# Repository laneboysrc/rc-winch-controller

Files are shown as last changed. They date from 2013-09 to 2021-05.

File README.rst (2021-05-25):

DIY controller an RC car winch
==============================

This project is for a winch controller for Radio Controlled cars that uses
channel 3 to operate the winch remotely.

Usage
=====

Connect the winch controller to channel 3 of your receiver.

Three seconds after you apply power to the controller the winch motor will play
a short tune. The sound will only play if a valid input signal has been
detected. Note that the sound generated by the motor may be very faint depending on your
winch.

To arm the switch, change the position of the channel 3 switch on your
transmitter five times within a short period of times. The winch motor
will now play a different tune of rising sounds indicatiting that it is
armed. While armed, the winch motor will be braked electrically.

To move the winch in one direction, change the position of the channel 3
switch once. To move the winch in the other direction, change the position
of the channel 3 switch twice within a short time.

To stop the winch moving toggle the position of the channel 3 switch.

Hardware
========

The winch hardware is basically a H-bridge motor driver controlled from a
tiny microcontroller.

The winch controller can be powered via the RC receiver, or from a separate
supply connected to the pins labeled + an - on the ICSP connector.

The main components are a Microchip PIC 12F1840 microcontroller, two
dual N- and P-Channel power FETs Fairchild FDS9934C, and a 3.3V LDO
(Microchip MCP1702, 1703 or similar).

A common 1/10th scale RC winch can lift about 1.5 kg at 6 Volts. The maxium
current we measured on our winch is 800 mA.

The schematics and a PCB layout are available in the `electronics <electronics/>`_ folder.

Bill of material:

::

    Qty Value            Device               Parts
    1   PIC12F1840       PIC12F1840 S08       U$2
    2   FDS9934          P/N MOSFET SO8       T1, T2
    1   MCP1702-3302     LDO 3V3 SOT23        U$1
    2   MMTB2222         NPN-TRANSISTOR SOT23 Q1, Q2
    2   1uF/16V          Capacitor SMD 1206   C1, C2
    1   0R               Resistor SMD 0603    R9 (can be replced with a solder bridge)
    6   4k7              Resistor SMD 0603    R1, R2, R3, R4, R7, R8
    2   47k              Resistor SMD 0603    R5, R6

The 2-layer PCB size is 22.05 x 27.43 mm (0.87 x 1.08 inches).

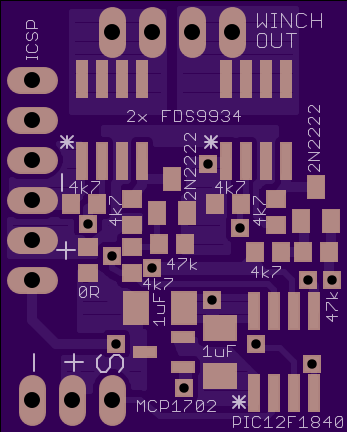
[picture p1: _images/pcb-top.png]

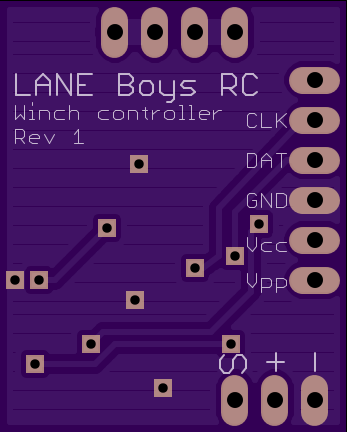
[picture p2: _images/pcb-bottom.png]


Gerber files for the PCB can be found in the `electronics <electronics/>`_ folder. The PCB can be
`ordered directly from OSHPark <http://www.oshpark.com>`_ in a minimum quantity of three.

Software
========

The firmware has been developed using SDCC version 3.3 and gpasm version 1.0.
GNU make is required for the build.

If you are compiling the software on a computer that does not have Unix-like
tools installed (e.g. Microsoft Windows) then you may need to adapt the
rm utility referenced in the Makefile (i.e. use "del" instead of "rm").

For convenience a pre-compiled HEX file is available for download `here <firmware/rc-winch-controller-servo.hex>`_.

The firmware comes in two variants: One that connects to channel 3 of a
RC receiver, and one with UART input which is meant to be utilized in
conjunction with the `LANE Boys RC DIY RC Light controller <http://laneboysrc.blogspot.com/2012/07/diy-car-light-controller-for-3-channel.html>`_.

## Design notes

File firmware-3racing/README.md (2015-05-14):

This folder contains firmware for the 3-Racing winch controller so
that it can be used with a 2-position switch.

The original 3-Racing winch controller works with a transmitter that has
a 3-position switch on CH3.

This firmware hooks in-between the receiver output and the 3-Racing winch
controller. It reads the CH3 2-pos switch info from the receiver and on
change of the switch outputs a servo signal simulating a 3-position switch.

After power on the winch is off. Every CH3 change modifies the servo
signal output to the 3-Racing controller:

Off         1500us
Winch out   2000us
Off         1500us
Winch in    1000us
Off         1500us
Winch out   2000us
...

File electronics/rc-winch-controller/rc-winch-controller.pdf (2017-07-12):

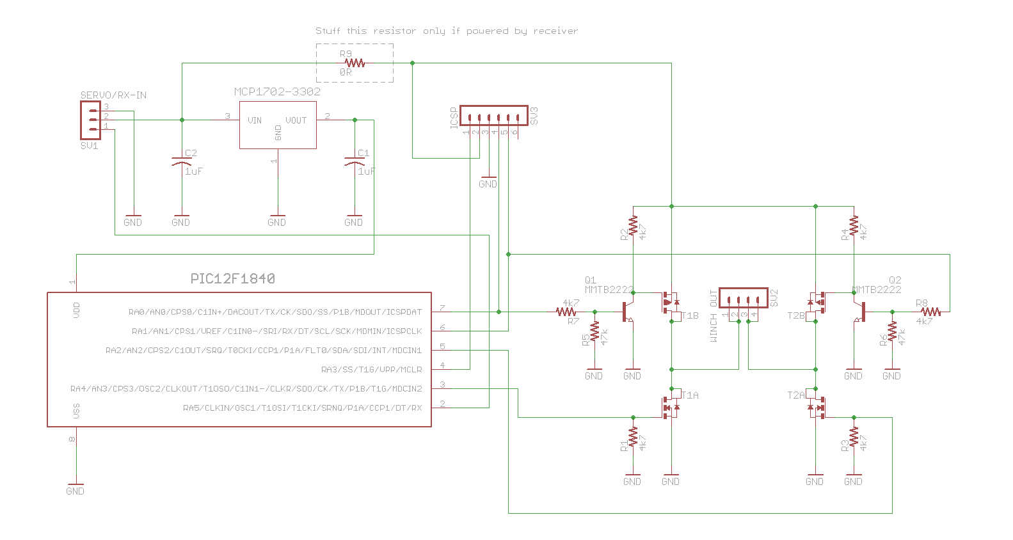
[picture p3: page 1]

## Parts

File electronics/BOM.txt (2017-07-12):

Part        Value              Package    Description
=============================  ========================================================
C1          1uF/16V            C1206K     CAPACITOR
C2          1uF/16V            C1206K     CAPACITOR
Q1          MMTB2222           SOT23      NPN TRANSISTOR
Q2          MMTB2222           SOT23      NPN TRANSISTOR
R1          4k7                R0603      RESISTOR
R2          4k7                R0603      RESISTOR
R3          4k7                R0603      RESISTOR
R4          4k7                R0603      RESISTOR
R5          47k                R0603      RESISTOR
R6          47k                R0603      RESISTOR
R7          4k7                R0603      RESISTOR
R8          4k7                R0603      RESISTOR
R9          0R                 R0603      RESISTOR
SV1         SERVO/RX-IN                   PIN HEADER
SV2         WINCH OUT                     PIN HEADER (optional)
SV3         ICSP                          PIN HEADER (optional)
T1          FDS9934            SO8        DUAL N AND P-CHANNEL ENHANCEMENT MODE MOSFET
T2          FDS9934            SO8        DUAL N AND P-CHANNEL ENHANCEMENT MODE MOSFET
U$1         MCP1702T-3302E/CB  SOT-23A
U$2         PIC12F1840         SO8        Microchip PIC12F1840

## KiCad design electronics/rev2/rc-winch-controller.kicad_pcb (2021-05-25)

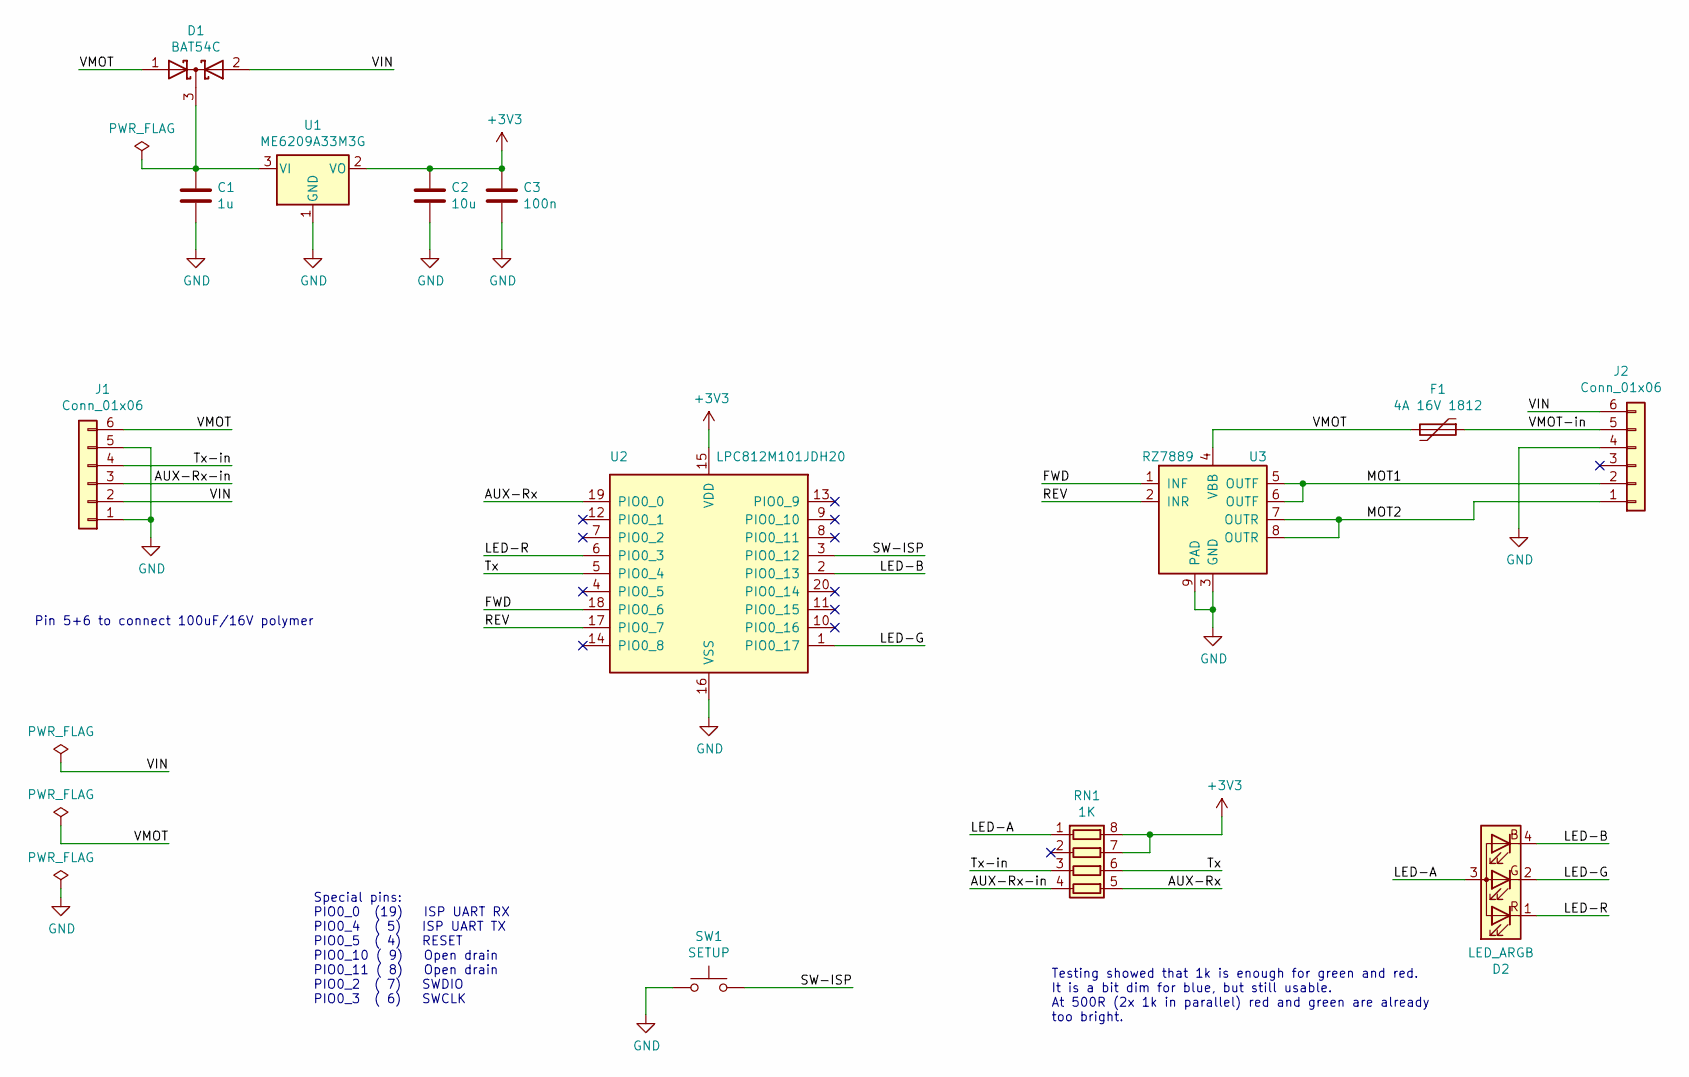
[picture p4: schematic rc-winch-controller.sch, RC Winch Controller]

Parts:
C1: 1u; C_0805_2012Metric
C2: 10u; C_0805_2012Metric
C3: 100n; C_0603_1608Metric
D1: BAT54C; SOT-23
D2: LED_ARGB; LED_RGB_XINGLIGHT_XL-2012RGBC
F1: 4A 16V 1812; Fuse_1812_4532Metric_Pad1.30x3.40mm_HandSolder
J1, J2: Conn_01x06; PinHeader_1x06_P2.54mm_Flat
RN1: 1K; R_Array_Convex_4x0603
SW1: SETUP; Tact switch 6x4x3
U1: ME6209A33M3G; SOT-23W
U2: LPC812M101JDH20; TSSOP-20_4.4x6.5mm_P0.65mm
U3: RZ7889; SOIC-8-1EP_3.9x4.9mm_P1.27mm_EP2.29x3mm_ThermalVias

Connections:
+3V3: C2.1, C3.1, RN1.7 (R2.2), RN1.8 (R1.2), U1.2 (VO), U2.15 (VDD)
/AUX-Rx: RN1.5 (R4.2), U2.19 (PIO0_0)
/AUX-Rx-in: J1.3, RN1.4 (R4.1)
/FWD: U2.18 (PIO0_6), U3.1 (INF)
/LED-A: D2.3 (A), RN1.1 (R1.1)
/LED-B: D2.4 (BK), U2.2 (PIO0_13)
/LED-G: D2.2 (GK), U2.1 (PIO0_17)
/LED-R: D2.1 (RK), U2.6 (PIO0_3)
/MOT1: J2.2, U3.5 (OUTF), U3.6 (OUTF)
/MOT2: J2.1, U3.7 (OUTR), U3.8 (OUTR)
/REV: U2.17 (PIO0_7), U3.2 (INR)
/SW-ISP: SW1.2, U2.3 (PIO0_12)
/Tx: RN1.6 (R3.2), U2.5 (PIO0_4)
/Tx-in: J1.4, RN1.3 (R3.1)
/VIN: D1.2 (A), J1.2, J2.6
/VMOT: D1.1 (A), F1.2, J1.6, U3.4 (VBB)
/VMOT-in: F1.1, J2.5
GND: C1.2, C2.2, C3.2, J1.1, J1.5, J2.4, SW1.1, U1.1 (GND), U2.16 (VSS), U3.3 (GND), U3.9 (PAD)
unnamed: C1.1, D1.3 (K), U1.3 (VI)

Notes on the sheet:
Special pins: PIO0_0 (19) ISP UART RX PIO0_4 ( 5) ISP UART TX PIO0_5 ( 4) RESET PIO0_10 ( 9) Open drain PIO0_11 ( 8) Open drain PIO0_2 ( 7) SWDIO PIO0_3 ( 6) SWCLK
Testing showed that 1k is enough for green and red. It is a bit dim for blue, but still usable. At 500R (2x 1k in parallel) red and green are already too bright.
Pin 5+6 to connect 100uF/16V polymer

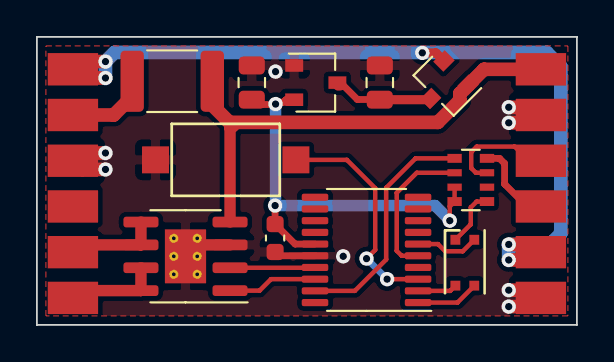
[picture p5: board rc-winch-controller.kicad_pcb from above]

Board: 2 copper layers, 30.0 x 16.0 mm, 13 parts (0 on the bottom side), 19 nets.

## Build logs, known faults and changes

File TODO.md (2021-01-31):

# Ideas for Mk2

* Up to 3S operation (12.6V)
* LEDs and push-button for configuration
* Inputs
    - Servo input 3-pos switch
    - Servo input 2-pos switch
    - External 3-pos switch
    - External 2-pos switch
    - External push-button (any difference from 2-pos switch?)
    - Internal push-button
    - Light Controller protocol
* Arming function
    * Can be disabled in the settings
    * Applies to all input modes except Light Controller
* Configurable motor reversal
    * Do we need that? User can just plug in the motor the other way around ...
* Firmware update
    * Hold button to start
* Configurable safety timeout for motor running
* Mini-ESC mode
    - 8 kHz to 16 kHz PWM frequency?
    - Drag brake adjustable?
    - Different modes: F/B/R, Crawler mode, F/B?
    - End-point learning
    - Channel reversing
    - Punch?

## Building blocks

* LPC812 16p (or QFN?)
* Use Wuxi RZ7899 or RZ7889 motor driver
* LDO 3V3
* 100uF polymer 16V 5x9mm
* Low-cost 3.3V-side buffer cap? 10u MLCC?
* Pushbutton
* External 2-pos switch connects to S/RX - GND
* External 3-pos switch connects to S/RX - Tx - GND
* RGB LED
* Power input
    * Allow various combinatoins:
        * Motor and electronics powered from servo connector
        * Motor and electronics powered from external supply
        * Motor powered from external supply, electronics powered from servo connector
    * Feed MCU from BAT54C! SOT-23
        * Motor-side use 6p connector with same jumper arrangement as on Mk4P/Mk4S

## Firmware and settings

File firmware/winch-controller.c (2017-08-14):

#include <pic12f1840.h>
#include <stdint.h>

static __code uint16_t __at (_CONFIG1) configword1 = _FOSC_INTOSC & _WDTE_OFF & _PWRTE_ON & _MCLRE_OFF & _CP_OFF & _CPD_OFF & _BOREN_OFF & _CLKOUTEN_OFF & _IESO_OFF & _FCMEN_OFF;
static __code uint16_t __at (_CONFIG2) configword2 = _WRT_OFF & _PLLEN_OFF & _STVREN_OFF & _LVP_OFF;


/*

Pin 7   RA0/ICSPDAT = High side left
Pin 6   RA1/ICSPCLK = High side right
Pin 5   RA2/CCP1  = Low side right (CCP1 for music!)
Pin 4   RA3/Vpp goes to ICSP
Pin 3   RA4 = Low side left
Pin 2   RA5/RX = Servo/UART Input

Music that the controller makes
===============================
- Startup sound
- Off to idle transition
- Idle to off transition


Playing a "song" through the motor
==================================

Single tones are generated by a PWM of 50% at the frequency of the sound.
A "song" comprises of individual notes, each note has a duration.
Between notes there can be pauses of a given duration.

Music notes go from 16.35 Hz to 4978.03 Hz according to
http://www.phy.mtu.edu/~suits/notefreqs.html
C3 to C5 (a smaller scale probably is enough) from 130.81 to 523.25 Hz
Maybe the best is to encode the musical note (there are 12 notes in an
octave) and have a table that has pre-calculated timer values for
the reqired frequency.

130.81 Hz (C3) -> 7645 us period = 3823 us half period
440 Hz (A4) -> 2273 us period = 1136 us half period
2093 Hz (C7) -> 478 us period = 239 us half period

If we allow for 4..1020 ms tone / pause durations (8 bits with 4ms resolution)
we need to decrement the "tone counter" every 4,096 ms. We can do that
reasonably accurate by accumulating an 8 bit value with a 16us resolution.
So at each interrupt we would add the number of "16us units" to our counter.
If it  overflows we decrement the tone counter. This way we should be able to
account for reasonably accurate tone durations regardless of the
note frequency.

If we use Timer1 for music we will not be able to output music at the
same time as measuring a servo pulse. This should not pose an issue
if the songs we play are short, and we can make the software stop while
the songs are playing.

We use Timer1 and CCP1 in compare mode. CCP1 is set-up to trigger
an interrupt on match and reset the counter. We toggle the output
in the interrup routine.

We run Timer1 with a 1 us clock. For every note we need the 16 bit compare
value. We need to also have the 16us based increment value, which
we can easily calculate out of the compare value (divide by 16 is ">> 4").

*/

#define MOTOR_OFF   0b00000000      // Motor ports are floating
#define MOTOR_BRAKE 0b00010100      // Motor ports are shorted for brake function
#define MOTOR_IN    0b00000101      // Direction for winching in
#define MOTOR_OUT   0b00010010      // Direction for winching out

// Enumeration for notes used in songs
#define C3 0
#define D3 1
#define E3 2
#define F3 3
#define G3 4
#define A3 5
#define B3 6
#define C4 7
#define D4 8
#define E4 9
#define F4 10
#define G4 11
#define A4 12
#define B4 13
#define C5 14
#define PAUSE 15
#define SONG_END 0xff

// Frequencies for each notes in Hz
// Source: http://www.phy.mtu.edu/~suits/notefreqs.html
#define F_C3 130.81
#define F_D3 146.83
#define F_E3 164.81
#define F_F3 174.61
#define F_G3 196.00
#define F_A3 220.00
#define F_B3 246.94
#define F_C4 261.63
#define F_D4 293.66
#define F_E4 329.63
#define F_F4 349.23
#define F_G4 392.00
#define F_A4 440.00
#define F_B4 493.88
#define F_C5 523.25

#define T_PAUSE 0xFFF   // Use 4096us as compare value for pause

#define SONG_STARTUP 0
#define SONG_ACTIVATE 1
#define SONG_DEACTIVATE 2
#define SONG_DUMMY_BRAKE 3

extern void Init_input(void);
extern void Read_input(void);

enum {
    WINCH_MODE_UNINITIALIZED = 0,
    WINCH_MODE_OFF = 0x80,
    WINCH_MODE_IDLE = 0x81,
    WINCH_MODE_IN = 0x82,
    WINCH_MODE_OUT = 0x83
} winch_mode = WINCH_MODE_UNINITIALIZED;

static unsigned char old_winch_mode = WINCH_MODE_UNINITIALIZED;
static volatile unsigned char note;
static volatile unsigned char duration;
static volatile unsigned char duration_increment;
static volatile unsigned char duration_counter;
static volatile unsigned char in_progress_flag;
static volatile unsigned char note_output_flag;


// Tables to look up the CCP1 compare values for a given note. High byte
// and low byte have a separate table for simplicity sake.
__code unsigned char notes_high[] = {
    ((unsigned int) (500000 / F_C3)) >> 8,
    ((unsigned int) (500000 / F_D3)) >> 8,
    ((unsigned int) (500000 / F_E3)) >> 8,
    ((unsigned int) (500000 / F_F3)) >> 8,
    ((unsigned int) (500000 / F_G3)) >> 8,
    ((unsigned int) (500000 / F_A3)) >> 8,
    ((unsigned int) (500000 / F_B3)) >> 8,
    ((unsigned int) (500000 / F_C4)) >> 8,
    ((unsigned int) (500000 / F_D4)) >> 8,
    ((unsigned int) (500000 / F_E4)) >> 8,
    ((unsigned int) (500000 / F_F4)) >> 8,
    ((unsigned int) (500000 / F_G4)) >> 8,
    ((unsigned int) (500000 / F_A4)) >> 8,
    ((unsigned int) (500000 / F_B4)) >> 8,
    ((unsigned int) (500000 / F_C5)) >> 8,
    ((unsigned int) T_PAUSE) >> 8
};

__code unsigned char notes_low[] = {
    ((unsigned int) (500000 / F_C3)),
    ((unsigned int) (500000 / F_D3)),
    ((unsigned int) (500000 / F_E3)),
    ((unsigned int) (500000 / F_F3)),
    ((unsigned int) (500000 / F_G3)),
    ((unsigned int) (500000 / F_A3)),
    ((unsigned int) (500000 / F_B3)),
    ((unsigned int) (500000 / F_C4)),
    ((unsigned int) (500000 / F_D4)),
    ((unsigned int) (500000 / F_E4)),
    ((unsigned int) (500000 / F_F4)),
    ((unsigned int) (500000 / F_G4)),
    ((unsigned int) (500000 / F_A4)),
    ((unsigned int) (500000 / F_B4)),
    ((unsigned int) (500000 / F_C5)),
    ((unsigned int) T_PAUSE)
};


__code unsigned char song_startup[] = {
    C4, 80000 / 4096,
    PAUSE, 40000 / 4096,
    F4, 80000 / 4096,
    PAUSE, 40000 / 4096,
    A4, 80000 / 4096,
    PAUSE, 40000 / 4096,
    C5, 160000 / 4096,
    PAUSE, 40000 / 4096,
    A4, 80000 / 4096,
    PAUSE, 40000 / 4096,
    C5, 240000 / 4096,
    SONG_END
};

__code unsigned char song_activate[] = {
    C4, 80000 / 4096,
    D4, 80000 / 4096,
    E4, 80000 / 4096,
    F4, 80000 / 4096,
    G4, 80000 / 4096,
    C4, 80000 / 4096,
    D4, 80000 / 4096,
    E4, 80000 / 4096,
    F4, 80000 / 4096,
    G4, 80000 / 4096,
    A4, 80000 / 4096,
    B4, 80000 / 4096,
    C5, 160000 / 4096,
    SONG_END
};

__code unsigned char song_deactivate[] = {
    C5, 80000 / 4096,
    B4, 80000 / 4096,
    A4, 80000 / 4096,
    G4, 80000 / 4096,
    F4, 80000 / 4096,
    C5, 80000 / 4096,
    B4, 80000 / 4096,
    A4, 80000 / 4096,
    G4, 80000 / 4096,
    F4, 80000 / 4096,
    E4, 80000 / 4096,
    D4, 80000 / 4096,
    C4, 240000 / 4096,
    SONG_END
};

// Not really a 'song', just a pause to prevent shoot-through before
// braking the winch
__code unsigned char song_dummy_brake[] = {
    PAUSE, 50000 / 4096,
    SONG_END
};

/*****************************************************************************
 Init_hardware()

 Initializes all used peripherals of the PIC chip.
 ****************************************************************************/
static void Init_hardware(void) {
    //-----------------------------
    // Clock initialization
    OSCCON = 0b01111010;    // 4x PLL disabled, 16 MHz HF, Internal oscillator

    //-----------------------------
    // IO Port initialization
    PORTA = 0;
    LATA = 0;
    ANSELA = 0;
    TRISA = 0b11101000;     // Make all ports that are not used for the motor input
    APFCON = 0b10000000;    // Use RA0/RA5 for UART TX/RX, CCP1 on RA2

    //-----------------------------
    // Initialize Timer1 for 1 MHz operation
    // Compare mode: special event trigger
    T1CON = 0b00100000;
    CCP1CON = 0b00001011;

    // Enable interrupts (though non specific is active at this point)
    PEIE = 1;
    GIE = 1;
}


/*****************************************************************************
 Play_song()

 Play a melody via the connected motor.
 This function only returns after the song has finished completely.

 A song is a sequence of notes and their duration. A special marker is used
 to signify a pause of a certain duration, another special marker indicates
 the end of the song. Songs are stored in ROM.
 ****************************************************************************/
void Play_song(unsigned char song) {
    const unsigned char *song_ptr;

    song_ptr = song_startup;
    if (song == SONG_ACTIVATE)
        song_ptr = song_activate;
    if (song == SONG_DEACTIVATE)
        song_ptr = song_deactivate;
    if (song == SONG_DUMMY_BRAKE)
        song_ptr = song_dummy_brake;

    // For each note in the song do ...
    while (*song_ptr != SONG_END) {
        // Load the note and its duration
        note = *song_ptr++;
        duration = *song_ptr++;

        // Retrive the on/off duration for the requested note
        CCPR1H = notes_high[note];
        CCPR1L = notes_low[note];

        // Calculate the 16 us units the on/off duration occupies so that
        // we can use the note frequency to time duration as well
        duration_increment =  (notes_high[note] << 4) + (notes_low[note] >> 4);

        // Start the Timer1 and enable the interrupt handing the frequency.
        in_progress_flag = 1;
        CCP1CON = 0b00001011;   // Compare mode: special event trigger
        CCP1IE = 1;
        TMR1ON = 1;

        // Wait until the interrupt completed playing the current note
        while (in_progress_flag != 0) {
            ; // wait ...
        }
    }
}


/*****************************************************************************
 Intr()

 Interrupt handler!

 The interrupt handler is triggered by CCP1 in special event mode.
 When the compare registers match the timer is reset and the interrupt is
 triggered.
 ****************************************************************************/
void Intr(void) __interrupt 0
{
    CCP1IF = 0;

    // Toggle the motor output unless we are dealing with a Pause
    // Note that we must turn the motor foward/backwards to stay at its current
    // position, otherwise it will spin in one direction
    // Note that we add motor-off inbetween to prevent MOSFET shoot-through.
    if (note != PAUSE) {
        ++note_output_flag;
        if ((note_output_flag & 0x03) == 0x01)
            LATA = MOTOR_IN;
        else if ((note_output_flag & 0x03) == 0x03)
            LATA = MOTOR_OUT;
        else
            LATA = MOTOR_OFF;
    }
    else {
        LATA = MOTOR_OFF;
    }

    // Add the time of the note on/off period in 16 us units to a counter.
    // If the counter overflows (16 us * 256 = 4.096 ms) decrement the
    // note duration. If the duration has reached zero we have finished
    // playing the note (or pause), so  we terminate further interrupts
    // and let the Play_song function know that we are finished.
    duration_counter += duration_increment;
    if (C != 0) {
        --duration;
        if (duration == 0) {
            LATA = MOTOR_OFF;
            CCP1IE = 0;
            TMR1ON = 0;
            in_progress_flag = 0;
        }
    }
}


/*****************************************************************************
 Process_winch()

 Turns the winch on/off depending on the requested winch mode, and play
 songs if needed.
 ****************************************************************************/
static void Process_winch(void) {
    if (winch_mode != old_winch_mode) {
        switch(winch_mode) {

        case WINCH_MODE_OFF:
            LATA = MOTOR_OFF;
            if (old_winch_mode != WINCH_MODE_UNINITIALIZED) {
                Play_song(SONG_DEACTIVATE);
            }
            break;

        case WINCH_MODE_IDLE:
            if (old_winch_mode == WINCH_MODE_OFF) {
                Play_song(SONG_ACTIVATE);
            }
            // Pause for a short time to prevent shoot-through in the MOSFETs,
            // then short-circuit the motor winding to brake electrically
            Play_song(SONG_DUMMY_BRAKE);
            LATA = MOTOR_BRAKE;
            break;

        case WINCH_MODE_IN:
            LATA = MOTOR_IN;
            break;

        case WINCH_MODE_OUT:
            LATA = MOTOR_OUT;
            break;

        default:
            LATA = MOTOR_OFF;
            break;
        }

        old_winch_mode = winch_mode;
    }
}


/*****************************************************************************
 main()

 No introduction needed ...
 ****************************************************************************/
void main(void) {
    Init_hardware();
    Init_input();

    // In order to not draw power straight away after power-on we delay
    // execution for 3 rounds of Read_input().
    // This was originally designed for the UART reader, where the UART
    // sender would send out commands once a second.
    // Other readers need to implement a delay function in their Read_input()
    // to achieve similar timings. WINCH_MODE_UNINITIALIZED could be used
    // to determine whether such delay is necessary.
    for (duration_counter = 0; duration_counter < 3 ; ++duration_counter) {
        Read_input();
    }

    Play_song(SONG_STARTUP);

    while (1) {
        Read_input();
        Process_winch();
    }
}

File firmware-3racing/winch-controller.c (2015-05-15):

#include <pic12f1840.h>
#include <stdint.h>

static __code uint16_t __at (_CONFIG1) configword1 = _FOSC_INTOSC & _WDTE_OFF & _PWRTE_ON & _MCLRE_OFF & _CP_OFF & _CPD_OFF & _BOREN_OFF & _CLKOUTEN_OFF & _IESO_OFF & _FCMEN_OFF;
static __code uint16_t __at (_CONFIG2) configword2 = _WRT_OFF & _PLLEN_OFF & _STVREN_OFF & _LVP_OFF;


/*

Pin 7   RA0/ICSPDAT     Servo output to 3-Racing winch
Pin 6   RA1/ICSPCLK     Servo input from receiver
Pin 5   RA2/CCP1        NC
Pin 4   RA3/Vpp         ICSP
Pin 3   RA4             NC
Pin 2   RA5/RX          NC
Pin 1   Vdd             +4.7V
Pin 8   Vss             GND

*/

#define SERVO_OUTPUT LATA0

extern void Init_input(void);
extern void Read_input(void);

enum {
    WINCH_MODE_UNINITIALIZED = 0,
    WINCH_MODE_OFF = 1,
    WINCH_MODE_OUT = 2,
    WINCH_MODE_OFF2 = 3,
    WINCH_MODE_IN = 4
} winch_mode = WINCH_MODE_UNINITIALIZED;

static volatile unsigned char duration_counter;


/*****************************************************************************
 Init_hardware()

 Initializes all used peripherals of the PIC chip.
 ****************************************************************************/
static void Init_hardware(void) {
    //-----------------------------
    // Clock initialization
    OSCCON = 0b01111010;    // 4x PLL disabled, 16 MHz HF, Internal oscillator

    //-----------------------------
    // IO Port initialization
    ANSELA = 0;
    LATA = 0b00000001;
    TRISA = 0b11111110;     // Make all ports except RA0

    //-----------------------------
    // Initialize Timer1 for 1 MHz operation
    T1CON = 0b00100000;
    CCP1CON = 0b00000000;   // Compare mode off
}


/*****************************************************************************
 Process_winch()

 Turns the winch on/off depending on the requested winch mode, and play
 songs if needed.
 ****************************************************************************/
static void Process_winch(void) {
    switch(winch_mode) {
        case WINCH_MODE_IN:
                CCPR1L = 1000 & 0xff;
                CCPR1H = 1000 >> 8;
            break;

        case WINCH_MODE_OUT:
                CCPR1L = 2000 & 0xff;
                CCPR1H = 2000 >> 8;
            break;

        case WINCH_MODE_UNINITIALIZED:
        case WINCH_MODE_OFF:
        case WINCH_MODE_OFF2:
        default:
                CCPR1L = 1500 & 0xff;
                CCPR1H = 1500 >> 8;
            break;
    }

    TMR1H = 0;              // Start the timer from 0
    TMR1L = 0;
    CCP1CON = 0b00001010;   // Enable compare match (CCP1IF bit is set, CCP1 pin unaffected)
    CCP1IF = 0;             // Clear the compare event flag

    TMR1ON = 1;             // Start timer 1
    SERVO_OUTPUT = 1;
    while (!CCP1IF);        // Wait for compare value reached
    SERVO_OUTPUT = 0;

    TMR1ON = 0;             // Stop timer 1
    CCP1CON = 0b00000000;   // Compare mode off
}


/*****************************************************************************
 main()

 No introduction needed ...
 ****************************************************************************/
void main(void) {
    Init_hardware();
    Init_input();

    while (1) {
        Read_input();
        Process_winch();
    }
}

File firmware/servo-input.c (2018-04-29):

#include <pic12f1840.h>

extern enum {
    WINCH_MODE_UNINITIALIZED = 0,
    WINCH_MODE_OFF = 0x80,
    WINCH_MODE_IDLE = 0x81,
    WINCH_MODE_IN = 0x82,
    WINCH_MODE_OUT = 0x83
} winch_mode;

static struct {
    unsigned ch3_initialized : 1;
    unsigned ch3_state : 1;
    unsigned ch3_last_state : 1;
    unsigned ch3_transitioned : 1;
} f = {0, 0, 0, 0};

static unsigned char ch3_clicks = 0;
static unsigned char ch3_click_counter = 0;

// All units are in 32.768 ms resolution
#define CH3_INITIALIZATION_TIMEOUT 90
#define CH3_BUTTON_TIMEOUT 12


/*****************************************************************************
 Service_soft_timer()

 Soft timer with a resolution of 32.768ms
 ****************************************************************************/
static void Service_soft_timer(void) {
    if (TMR2IF) {
        TMR2IF = 0;

        // Decrement ch3_click_counter if it is running
        if (ch3_click_counter) {
            --ch3_click_counter;
        }
    }
}


/*****************************************************************************
 Init_input()

 Called once during start-up of the firmware.
 ****************************************************************************/
void Init_input(void) {
    /* Use Timer2 as soft timer with an interval of 32.768ms. This is half
       of what we would like to have, so software has to adjust for it.
    */
    PR2 = 0xff;
    T2CON = 0b00111111;     // 1:8 post scaler; timer on; Prescaler is 64
}


/*****************************************************************************
 Read_input

 Called once per mainloop to read the input signal.
 This function shall set the global variable winch_mode depending on the
 state transition logic desired.
 ****************************************************************************/
void Read_input(void) {
    unsigned int ch3;

    // If we are starting up delay this function for approx 3 seconds.
    // This way we don't energize the motor (music!) straight away during
    // power-up, causing spikes in the system while the power supply is still
    // stabilizing.
    if (winch_mode == WINCH_MODE_UNINITIALIZED) {
        ch3_click_counter = CH3_INITIALIZATION_TIMEOUT;
        while (ch3_click_counter) {
            Service_soft_timer();
        }
    }

    Service_soft_timer();


    // ##################################
    // Read the CH3 servo input into the variable ch3 (time value in us)
    TMR1H = 0;
    TMR1L = 0;
    CCP1CON = 0b00000000;   // Compare mode off

    // Wait until servo signal is LOW
    // This ensures that we do not start in the middle of a pulse
    while (RA5 != 0) ;

    // Wait until servo signal is high; start of pulse
    while (RA5 != 1) ;

    // Start the time measurement
    TMR1ON = 1;

    // Wait until servo signal is LOW again; end of pulse
    while (RA5 != 0) ;

    // Start the time measurement
    TMR1ON = 0;

    // Check if the measured pulse time is between 600 and 2500 us. If it is
    // outside we consider it an invalid servo pulse and stop further execution.
    ch3 = (TMR1H << 8) | TMR1L;

    if (ch3 < 600 || ch3 > 2500) {
        return;
    }


    // Apply a hysteresis function: If the servo input was "high" during
    // the last valid measurement, the value must drop below 1375 us before it
    // is considered "low".
    // If it was "low" during the last measurement it must rise above 1625 us
    // before it is considred "high" again.
    // This assumes that the servo pulses are centered around 1500us.
    if (f.ch3_last_state) {
        if (ch3 < 1375) {
            f.ch3_state = 0;
        }
        else {
            f.ch3_state = 1;
        }
    }
    else {
        if (ch3 > 1625) {
            f.ch3_state = 1;
        }
        else {
            f.ch3_state = 0;
        }
    }

    // If it is the first measurement after power-up we save the value
    // as initial value and consider the firmware initialized.
    if (winch_mode == WINCH_MODE_UNINITIALIZED) {
        f.ch3_last_state = f.ch3_state;
        winch_mode = WINCH_MODE_OFF;
    }

    // Determine whether CH3 has been toggled
    f.ch3_transitioned = 0;
    if (f.ch3_state != f.ch3_last_state) {
        f.ch3_last_state = f.ch3_state;
        f.ch3_transitioned = 1;
    }

    // If CH3 has been toggled add a click and (re-) start the click timeout.
    // If the winch is running turn it off straight away.
    if (f.ch3_transitioned) {
        ++ch3_clicks;
        ch3_click_counter = CH3_BUTTON_TIMEOUT;

        if (winch_mode == WINCH_MODE_IN  ||  winch_mode == WINCH_MODE_OUT) {
            winch_mode = WINCH_MODE_IDLE;
            // Set an invalid clicks number to ignore multiple clicks
            ch3_clicks = 99;
        }
    }

    if (ch3_clicks == 0) {          // Any buttons pending?
        return;                     // No: done
    }

    if (ch3_click_counter) {        // Double-click timer expired?
        return;                     // No: wait for more buttons
    }


    // Implement the business logic:
    // 5 clicks activate/deactivate the winch
    // 1 click: winch in if winch is active
    // 2 clicks: winch out if winch is active
    if (ch3_clicks == 1) {
        if (winch_mode == WINCH_MODE_IDLE) {
            winch_mode = WINCH_MODE_IN;
        }
    }
    if (ch3_clicks == 2) {
        if (winch_mode == WINCH_MODE_IDLE) {
            winch_mode = WINCH_MODE_OUT;
        }
    }
    if (ch3_clicks == 5) {
        if (winch_mode == WINCH_MODE_IDLE) {
            winch_mode = WINCH_MODE_OFF;
        }
        else {
            winch_mode = WINCH_MODE_IDLE;
        }
    }
    ch3_clicks = 0;
}

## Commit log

2013-05-17 Add schematics and libraries Eagle
    [rc-winch-controller.sch]
2013-05-17 Add library for PIC12F1840
    [rc-winch-controller.sch]
2013-05-20 Continue working on the schematic
    [rc-winch-controller.sch]
2013-05-20 Start on the board layout
    [rc-winch-controller.brd, rc-winch-controller.sch]
2013-05-20 Modify board vias
    [rc-winch-controller.brd]
2013-05-20 Fix schemtic for P-channel FET being reversed
    [rc-winch-controller.brd, rc-winch-controller.sch]
2013-05-21 Update MOSFET to include both drain pins
    [rc-winch-controller.brd, rc-winch-controller.sch]
2013-05-21 Add jumper resistor to be able to switch between receiver power and external power
    [rc-winch-controller.brd, rc-winch-controller.sch]
2013-05-21 Finalize board layout
    [rc-winch-controller.brd, rc-winch-controller.sch]
2013-06-11 Remove tPlace and bPlace from CAM file to remove annoying markers for connectors
2013-06-11 Improve the board layout
    [rc-winch-controller.brd, rc-winch-controller.sch]
2013-06-11 Add markers for IC pin 1 and fix silkscreen hitting solder mask
    [rc-winch-controller.brd]
2013-06-11 Add bottom silk screen
    [rc-winch-controller.brd]
2013-07-04 Start implementation of the winch controller, uart reader
2013-07-05 Layout and Gerber for version sent to OSHPark
2013-07-08 Add rudimentary motor code
2013-07-15 Add some thoughts regarding making of music with the motor.
2013-07-16 Add test code using compare mode on TIMER1 to toggle RA2 with 440 Hz
2013-07-24 Add UART error handling
2013-08-19 Use MOTOR macros instead of direct ports for song playing
2013-09-04 Make motor sound by running the motor forward and backwards instead of off and on
2013-09-05 Wait for 3 commands before initializing the winch.
    This ensures that we don't immediately draw a lot of current
    at start-up
2013-09-09 Start working on the servo input
    Just copied ASM code from the light controller.
2013-09-09 Add build rules for servo version of the winch controller
2013-09-09 Implement servo reading and normalization, incl. hysteresis
2013-09-10 Fix servo input, not it is working fine.
    [servo-input.c, winch-controller.c]
2015-05-15 Bugfix after testing, now fully working
    [servo-input.c, winch-controller.c]
2017-07-12 Add PDF version of the schematics
2017-07-12 Add dedicated BOM file and add capacitor voltage requirement
2017-08-14 Fix MOSFET shoot-through and ignore commands not meant for the winch
    [winch-controller.c]
2018-04-29 Make servo input work again
    Was broken when we changed the UART commands ...
    [servo-input.c]
2021-01-24 Start on Rev2 PCB
    [rc-winch-controller.kicad_pcb, rc-winch-controller.sch]
2021-01-25 Update PCB
    [rc-winch-controller.kicad_pcb, rc-winch-controller.sch]
2021-01-30 Update 3D models
    [rc-winch-controller.kicad_pcb]
2021-01-31 Update layout and silkscreen
    [rc-winch-controller.kicad_pcb, rc-winch-controller.sch]
2021-01-31 Tweak placement, layout and silk screen
    [rc-winch-controller.kicad_pcb]
2021-02-11 Change MCU to TSSOP 20 version
    [rc-winch-controller.kicad_pcb, rc-winch-controller.sch]
2021-02-12 Fix LED footprint and current limiting resistor
    1k is enough for red and green.
    It is a bit dark for blue, but 500R is too bright
    for red and green.
    [rc-winch-controller.kicad_pcb, rc-winch-controller.sch]
2021-02-14 Improve layout
    [rc-winch-controller.kicad_pcb, rc-winch-controller.sch]
2021-05-25 Remove YouTube video
    [rc-winch-controller.kicad_pcb]
